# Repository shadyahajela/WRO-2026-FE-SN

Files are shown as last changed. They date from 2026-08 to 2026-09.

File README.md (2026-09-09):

Team Sub-Atomica
====

This repository contains the engineering documentation and our journey of building an autonomous vehicle to compete at the 2026 WRO Future Engineers competition.

<p align="center">


## Introduction

We are Team Sub-Atomica, Niva, Jeevesh and Shadya. We are united by a passion for STEM, Electronics, coding and jalapeño poppers. We wanted to bring our jouney to many others with the same passions and inspire teenagers around the world. To us its more than just coding or building, its the experiences and connections along the way.


159C16BD-3B52-4F8A-85BE-AFA5FE405926 (1)
IMG_6102 (1)

## Robot 

Our robot is called Jadoo which means magic in Hindi. The name comes from a popular movie character who is also an alien and can do Jadoo. The drive base of our robot kind of looked like an alien head, so we named it after our favorite alien character.

### Robot images







**Dimensions**

| **Specification** | **Measurement** |
|---|---|
| **Width** | 12 cm |
| **Length** | 23 cm |
| **Height** | 17 cm (Without wire) |
| | 20 cm (With Camera wire) |
| **Weight** | About 800 grams |
          
The Width helps to get around tight areas and the height gives a low base with a more balanced center of gravity all while being easy to maneuver due to the length. 

## Open challenge videos
Watch the video (https://www.youtube.com/watch?v=8OkpqqfYOhU)

## Obstacle challenge video
Watch the video (https://www.youtube.com/watch?v=r0wWpeo_AAc)

## Content

* `t-photos` contains photos of the team.
* `v-photos` contains 6 photos of the vehicle (from every side, from top and bottom)
* `video` contains the video.md file with the link to a video where driving demonstration exists
* `schemes` contains one or several schematic diagrams in form of JPEG, PNG or PDF of the electromechanical components illustrating all the elements (electronic components and motors) used in the vehicle and how they connect to each other.
* `src` contains code of control software for all components which were programmed to participate in the competition
* `models` is for the files for models used by 3D printers, laser cutting machines and CNC machines to produce the vehicle elements. If there is nothing to add to this location, the directory can be removed.
* `other` is for other files which can be used to understand how to prepare the vehicle for the competition. It may include documentation how to connect to a SBC/SBM and upload files there, datasets, hardware specifications, communication protocols descriptions etc. If there is nothing to add to this location, the directory can be removed.

# 1. Mobility Management

To build a self-driving car we need to build a car.

Objectives:

As per the rules, the car must have a steering mechanism and the rear axle driven by a motor.
Our team also wanted the car to be stable and fast (and colorful if we can help it).

## 1.1 Drive System
**Drive Motor:** JGA25-371 DC Motor with Hall-encoder. 
  <table>
  <tr>
    <td align="center" width="300" >
      
    </td>
    <td>
      <h3>Specifications:</h3>
      <ul>
        <li>Voltage: 12V </li>
        <li>No-load Speed: 620RPM </li>
        <li>Stall Torque: 4.2kg/cm</li>
        <li>Current: 0.046A</li>
        <li>Gear Ratio: 21.3:1</li>
      </ul>
    </td>
  </tr>
  </table>

 **Selection Reasoning** 

+ Built-in encoder, allowing for precise movement and less wiring hassle.
+ High torque for pushing the robot with vigor and avoiding stalling.

The JGA25-371 motor was selected because it combines high torque with integrated encoder feedback, providing both the power and precision required for the WRO Future Engineers competition. The 620 RPM gives enough torque to have a fast robot and have enough control for parking. We calculated torque required to pull our robot and to start it. Additionally the hall encoder provides real-time feedback for closed-loop control, allowing the robot to accurately measure wheel rotation, regulate speed, and maintain consistent movement especially during parking. 



*Image pinpoints exact location of torque calculations.(for full image look for Torque and speed reasoning)*
<br/>

 **Considerations:**
  An alternative would be a NEMA 17 stepper motor, which can provide precise speed and position control. However, the NEMA 17 is larger and heavier, and would require a more complex driver setup, making it less suitable for our robot. The JGA25-371 was chosen instead because it provides sufficient speed and torque while being more compact and easier to integrate.

### Differential

We used a metal WLTOYS 144001 differential in our robot, allowing the left and right rear wheels to rotate at different speeds during turns, reducing tire scrub and improving turning efficiency. This provides smoother cornering by distributing torque between both wheels and compensating for the different distances they travel. The differential improves maneuverability and stability during the Obstacle Challenge and parallel parking, where precise and repeatable movement is essential, while its metal construction provides durability under drivetrain loads.
  
  <table>
  <tr>
    <td align="center" width="300" >
      
    </td>
    <td>
      <h3>Specifications:</h3>
      <ul>
        <li>Differential Type: Planetary bevel-gear differential</li>
        <li>Material: Metal</li>
        <li>Application: 1:14 RC vehicles</li>
        <li>Drive Configuration: Rear-wheel drive</li>
        <li>Compatibility: 5 mm drive cups (custom coupled to LEGO axle)</li>
      </ul>
    </td>
  </tr>
  </table>

  **Mounting:**

  * Installed using an inset groove system in the chassis screwed to a detachable 3D-printed motor differential housing clamp that is placed above the differential gear compartment. This will allow for future changes to accommodate different motors and gears if the need arise.

    

  * Wires connected to Arduino Nano and Motor Driver.
  * Spike Prime wheels fitted onto the LEGO motor axle.

## 1.2 Steering System

**Steering:** Initially Parallel Steering, then changed to Ackermann Steering Geometry, prototyped with LEGO technic parts and later made with 3D printed parts. Ackermann was especially important for obstacle navigation and parking, where precise control and a small turning radius are essential. We also considered parallel steering because it was simpler to implement, but chose Ackermann as a calculated risk for its improved maneuverability. Our implementation uses a custom 3D-printed Ackermann steering mechanism, we used Onshape to experiment with different pivot points, linkage positions, and steering angles throughout the design process.

Through 2 iterations, we shortened both rods and increased the length of the side rods to achieve a smaller turning radius while keeping the mechanism compact. In our first iteration we made our tabs 2mm longer and the neck of the robot smaller, this gave us a 15 degree increase in our turning radius. We also experimented with shortening the rods to make our wheels streamlined and finalized with 9.53cm for the long shaft and 8.5cm for the short one. A major constraint was the chassis neck, which limited the steering angle because the wheels could collide with it. We therefore cut part of the chassis around the steering area to provide sufficient clearance.

**Calibration and Implementation:**
To achieve accurate and consistent steering, we used a combination of CAD adjustments and physical testing:

* Different servo positions, linkage lengths, and steering angles were tested in Onshape to determine the most suitable configuration.
* The physical steering assembly was then tested by turning the wheels fully in both directions and checking for smooth, consistent movement.
* Based on the test results, we modified the CAD model and repeated the process until the steering geometry provided the desired range of motion and wheel           alignment.
* The final Onshape design was then used to produce the 3D-printed steering assembly.





*This was an early prototype of the Ackerman Steering model before we added it to the first iteration of our Lego car chassis.*

### Steering Motor

We chose the MG90S Micro Servo for precise steering and weight reduction. The compact size and PWM interface make the MG90S easy to integrate and control using the Arduino Nano. It provides sufficient torque to steer the front wheels accurately and responsively. Its fast response and metal gear construction provide reliable and stable steering during turns and lane changes. The MG90S is widely used in hobby robotics, making replacement parts, mounting hardware, and documentation readily available. Additionally while testing it with our code for control we were able to make it work 90% of the time, upon investigating we found a fault with the power system in the testing module which we solved by adjusting our wires. 

  <table>
  <tr>
    <td align="center" width="300" >
      
    </td>
    <td>
      <h3>Specifications:</h3>
      <ul>
        <li>Voltage: 4.8V-6V </li>
        <li>Operating Speed: 0.1 s/60° at 4.8 V, 0.08 s/60° at 6 V</li>
        <li>Stall Torque: 1.8 kg·cm at 4.8 V, 2.2 kg·cm at 6 V</li>
        <li>Current: 0.010A</li>
        <li>Rotation Range: Approximately 180° (90° in each direction)</li>
      </ul>
    </td>
  </tr>
  </table>

**Mounting:**

* Screwed into a platform plate in front of the chassis, connected to the steering mechanism.

  

**Considerations:**
An alternative would be the MG996R servo, which provides higher torque and more durable metal gears. However, it is larger and requires more power than the MG90S, which would require modifications to our chassis and power system. The MG90S was chosen instead because it is more compact and sufficient for our steering system.

## 1.3 Chassis Design

| Dimension | Value (mm) | Reason |
| --- | --- | --- |
| Width | 120 | Component fit (Arduino, voltage converter and battery in line horizontally) |
| Length | 230 | Tight turns and component fit |
| Height | 200 | (Including camera wire) |

### Design Overview:

**Iteration 1: LEGO**






Aspects acheived:
* A functioning robot capable of performing the game to a certain degree of efficiency.
* Experiment with a new camera angle.                                     

Drawbacks:
* Tall and bulky design paired with a narrow body produced a high center of gravity and minimal support, making the robot unstable on quick turns and slower on straights.
* The low camera angle caused loss of depth perception, we we decided to completely reengineer it. 
* LEGO Technic design limited freedom of customizability, forcing any 3D printed parts to align to a LEGO frame.
* Limited range of movement for LEGO Ackermann steering system, constraining turns to 40 degrees to either side.
* Terrible tolerances (byproduct of using LEGO) result in constant plastic grinding in rear drive system.
* Inefficient component layout leaving much wasted space and area for drag

**Iteration 2: 3D Printed Parts and LEGO fusion:**



Aspects achieved/retained:
* Customizability of component mounting, such as custom in-built mounts for the IMU, DC Motor, etc.
* Expanded range of movement for newly 3D printed Ackermann steering system, allowing turns up to 55 degrees to either side.
* Improved tolerances and a switch from LEGO to metal differential remove the grinding in the read drive system.
* Optimized component layout for maximum space usage and minimal drag-creating parts.

Drawbacks:
* LEGO camera mount restrains pinpoint mount changes to find optimal camera angle.
* LEGO servo mount is unnecessarily complex and is not fixed precisely, allowing for small movements when the servo moves.
* Slightly imprecise tolerances for rear differential drive system, resulting in jerky movement and inconsistent torque and speed.

**Iteration 3: Fully 3D Printed Chassis:**



Aspects achieved/retained:
* 3D printed camera mount allows for custom mounting; iteration testing resulted in us finding the optimal camera angle and height.
* 3D printed servo mount is a simple, single piece mount that effectively zeros servo shaking.
* Perfected tolerances in the rear differential drive system allow the motor to turn the rear axle efficiently with little energy lost and constant torque and speed.
* Customizability of component mounting, such as custom in-built mounts for the IMU, DC Motor, etc.
* Expanded range of movement for Ackermann steering system, allowing turns up to 55 degrees to either side.
* Optimized component layout for maximum space usage and minimal drag-creating parts.

Accepted Trade-Offs:
* Overall shape of the robot is not streamlined and produces drag, but minimal enough that it barely affects performance.
* Minimal space for wire management, wires don't affect functions of the robot so its accepted.

Our chassis was designed on Onshape and printed using Carbon fiber, as it is light and resistant to snapping, which helps in thin and high tension areas like the neck of our robot. Other than the chassis itself the other 3D printed components use PLA and are designed on Onshape as well.

## 1.4 Torque and Speed reasoning



Our torque and speed reasoning lists the given parameters, we are able to calculate the max speed, the robots acceleration as well as the gives the minimum torque required to move our robot, allowing us to control speed. We are also able to calculate the cruising torque and stall torque which we used for selecting our motor. Based on our robot's total mass of 0.8 kg and wheel diameter of 0.056 m, we calculated a required motor torque of approximately 0.0117 N·m during acceleration, which is well within our motor's stall torque of 0.0833 N·m, giving a safety margin of roughly 7x (required torque is only ~14% of available stall torque).

# 2. Power Systems and Hardware Architecture

For the car to know what its doing, we need input and power.

Objective: 
  - Select the right hardware / electronic components for the entire sensor input processing and actuator control in real-time 
  - Supply adequate power to all these components

## 2.1 Power Source

**Battery:** 3 Cell Lithium Battery

<table>
  <tr>
    <td align="center" width="300" >
      
    </td>
    <td>
      <h3>Specifications:</h3>
      <ul>
        <li>Nominal Voltage: 11.1V</li>
        <li>Fully Charged Voltage: 12.6V</li>
        <li>Capacity: 3000 mAh</li>
        <li>Discharge Rate: 30 C</li>
        <li>Maximum Continuous Current: 90 A</li>
        <li>Battery Type: Lithium-Polymer</li>
      </ul>
    </td>
  </tr>
  </table>

The power system is essential to the robot’s ability to operate reliably throughout the competition. Our robot is powered by a 3-cell (3S) Lithium Polymer (LiPo) battery. The battery provides a nominal voltage of 11.1 V and a fully charged voltage of 12.6 V. Its high discharge capability allows it to supply sufficient current to the motors and other components. The battery’s high energy density provides a good balance between runtime, weight, and available power, making it well suited for a mobile competition robot. A rocker switch is connected directly to the power source independent of the code to switch on and off the robot. 

The JGA25-371 motor operate from the 12V supply provided by the battery, while the L298N motor driver regulates the power delivered to the motors based on commands from the Arduino Nano. The higher voltage of the 3S battery allows the motors to operate without requiring a step-up converter, simplifying the power system and reducing unnecessary conversion losses. A step-down converter is used to reduce the battery voltage to the appropriate levels required by the Raspberry Pi 5, Arduino Nano, camera, IMU, and other electronics. This separates the high-current motor supply from the lower-voltage electronics while allowing the entire robot to be powered from a single battery.

**Motor Driver:** L298N
  
  <table>
  <tr>
    <td align="center" width="300" >
      
    </td>
    <td>
      <h3>Specifications:</h3>
      <ul>
        <li>Driver Type: Dual H-Bridge</li>
        <li>Motor supply voltage: 5–35 V</li>
        <li>Maximum current: 2 A per channel</li>
        <li>PWM speed control</li>
        <li>Bidirectional motor control</li>
        <li>Overtemperature protection</li>
      </ul>
    </td>
  </tr>
  </table>

We chose the L298N motor driver because it provides reliable control of our JGA25-371 DC motor while being compatible with the Arduino Nano. It supports the 12V supply from our 3-cell LiPo battery and allows the Arduino to control motor direction and speed through its PWM inputs. This provides a simple and reliable connection between the robot’s power system and drivetrain, making it well suited for our differential drive system. The driver has a voltage drop in its internal transistors which causes us to not achieve its full potential, but we were willing to make a trade-off as we were content with what we were able to use it for.  

OLD MOTOR DRIVER IMAGE: DRV8871



We used DRV8871 in earlier iterations of the robot because of its compactness and its single motor control. However, it kept burning out due to motor feedback coming back to the driver. Motor feedback occurs when a motor is forced to move, and was probably caused by the constant pulling of the robot we did when testing. After further research, we found out that this feedback was a common problem with the DRV8871, so we decided to move to the L298N motor driver. Although it is much larger and bulkier, we had considerable space for the motor driver so it wasn't an issue. The L298N also has a heatsink, so overheating is not a problem.

## 2.2 Sensor and Camera
  
  **SainSmart Wide-Angle Camera:** 

  <table>
  <tr>
    <td align="center" width="300" >
      
    </td>
    <td>
      <h3>Specifications:</h3>
      <ul>
        <li>Resolution: 5MP (2592 × 1944)</li>
        <li>Image Sensor: OV5647</li>
        <li>Field of View: 160°</li>
        <li>Interface: CSI</li>
        <li>Video: 1080p @ 30 FPS, 720p @ 60 FPS, 640 × 480 @ 60/90 FPS</li>
        <li>Dimensions: 25 × 24 × 9 mm</li>
      </ul>
    </td>
  </tr>
  </table>

**Selection Reasoning:** 

- 160° wide field of view captures more of the course, reducing blind spots and improving environmental awareness.
- 5MP resolution provides enough detail to reliably distinguish course features and colored markers.
- 1080p at 30 FPS provides responsive visual data for real-time image processing and object detection.
- Compact and lightweight design reduces its impact on vehicle weight and balance while allowing flexible mounting.

This setup provides a 160° wide-angle view that increases the robot's visual coverage during both the Open Challenge and Obstacle Challenge. The camera supplies visual information about walls, pillars, colored markers, parking spaces, and lane lines, which is combined with other sensor data to support navigation and decision-making. The main tradeoff is balancing wider coverage with image processing requirements, so the selected resolution and frame rate provide sufficient detail and responsiveness without unnecessarily increasing processing demands.

The camera is mainly used for the following tasks:

- Detect and determine wall positions.
- Identify pillar colors and types.
- Recognize parking zones.
- Track path lines and boundaries.

**BNO055 Inertial Measurement Unit (IMU):** 

<table>
  <tr>
    <td align="center" width="300" >
      
    </td>
    <td>
      <h3>Specifications:</h3>
      <ul>
        <li>Sensor Type: 9-axis IMU (3-axis accelerometer, 3-axis gyroscope, 3-axis magnetometer)</li>
        <li>Processor: ARM Cortex-M0+ with integrated Bosch sensor-fusion firmware</li>
        <li>Interfaces: I²C, UART</li>
        <li>Operating Voltage: 3.3V</li>
        <li>Key Features: Absolute orientation, linear acceleration, gravity vector, magnetic heading, temperature sensing, and motion detection</li>
      </ul>
    </td>
  </tr>
</table>

**Selection Reasoning:** 

Considering we wanted to have a relative compass to reduce additional code in the Arduino, we chose the BNO055. The BNO055 is a compact 9-axis IMU that combines a3-axis accelerometer, 3-axis gyroscope, and 3-axis magnetometer with an onboard processor for sensor fusion. It provides orientation data such as heading,       Euler angles, linear acceleration, and gravity direction, reducing the need for complex external calculations.
    
We mounted the BNO055 near the center of the chassis to provide stable and consistent measurements. It communicates with the Arduino Nano through the I²C interface, continuously providing real-time orientation and angular velocity data. This helps the robot maintain an accurate heading and make smoother steering adjustments, which are especially important during obstacle navigation.  
  
## 2.3 Processing Units

**Single Board Computer: Raspberry Pi 5**

  <table>
  <tr>
    <td align="center" width="300" >
      
    </td>
    <td>
      <h3>Specifications:</h3>
      <ul>
        <li>Processor: Broadcom BCM2712</li>
        <li>CPU: Quad-core Arm Cortex-A76 (2.4 GHz)</li>
        <li>Power: 5 V / 5 A USB-C</li>
        <li>RAM: 8 GB LPDDR4X</li>
        <li>USB Ports: 2 × USB 3.0, 2 × USB 2.0</li>
        <li>Video Output: Dual micro-HDMI (60fps)</li>
      </ul>
    </td>
  </tr>
  </table>

*Subsystem Integration:*
The Raspberry Pi 5 acts as the robot’s primary processing unit, handling high-level decision-making, image processing, and sensor-data integration. Its processing capability allows it to run real-time vision, mapping, obstacle detection, and path-planning tasks while communicating with the Arduino Nano for low-level control.

*Hardware and Software Architecture:*
The Raspberry Pi 5’s quad-core Arm Cortex-A76 CPU and 8GB of RAM provide sufficient processing performance for the computational demands of the robot. Its compact form factor also allows it to be mounted directly onto the chassis without significantly increasing the vehicle’s size or weight. It communicates with the Arduino Nano through a serial connection, creating a modular architecture where high-level processing and low-level control are separated.

*Iterations and Trade-Offs:*
We initially tested a Raspberry Pi 4 to reduce power consumption, but testing showed that its lower processing performance caused slower image processing and reduced responsiveness during real-time vision and navigation tasks. We therefore changed to the Raspberry Pi 5, accepting higher power consumption in exchange for significantly improved processing performance and more reliable real-time operation.

*Risk Analysis and Reliability:*
Using the Raspberry Pi 5 reduces the risk of processing bottlenecks affecting navigation and vision performance. Separating high-level processing from the Arduino Nano’s low-level control also prevents computationally intensive tasks from directly interfering with motor and steering control, improving overall system reliability.

**Microcontroller:** Arduino Nano

  <table>
  <tr>
    <td align="center" width="300" >
      
    </td>
    <td>
      <h3>Specifications:</h3>
      <ul>
        <li>ATmega328P 8-bit microcontroller</li>
        <li>32 KB flash memory</li>
        <li>2 KB SRAM</li>
        <li>16 MHz clock speed</li>
        <li>22 multi-function I/O pins</li>
        <li>UART, I²C, and SPI communication</li>
      </ul>
    </td>
  </tr>
  </table>
  
*Subsystem Integration:* 

 The Arduino Nano was selected as the robot’s low-level controller to handle time-sensitive tasks such as motor control, steering, and encoder/sensor input. This architecture separates high-level decision-making from low-level control, allowing the Raspberry Pi 5 to focus on vision processing, navigation, and path planning while the Arduino maintains consistent motor and steering responses.

*Hardware and Software Architecture:*

The Arduino Nano communicates with the Raspberry Pi 5 through a serial connection, creating a modular hardware and software architecture. This reduced the risk of timing conflicts caused by running motor-control tasks alongside computationally intensive processes on the Raspberry Pi. It also allows each subsystem to be tested independently, making troubleshooting and future modifications easier. It also displays steering values on the 1.12" OLED screen, we use it for understanding what the robot is thinking and troubleshoot. 

*Iterations and Trade-Offs:*

Our initial design used a microbit, but research showed that the Arduino Nano offered greater flexibility for external hardware and simpler bidirectional communication with the Raspberry Pi 5. We therefore changed to the Arduino Nano, trading the microbit’s built-in buttons and LEDs for improved subsystem integration and expandability. The control system was then iteratively tested and adjusted to improve motor response, steering accuracy, and communication reliability. Using a dedicated microcontroller introduced additional hardware and communication complexity, but provided more predictable real-time control and reduced the dependence of critical drivetrain functions on the Raspberry Pi’s processing workload.

*Risk Analysis and Reliability:*

This subsystem architecture improves reliability by isolating critical low-level control from higher-level software. If the vision or navigation software requires significant processing, the Arduino can continue executing motor and steering commands without relying on continuous high-level computation. This separation therefore supports more consistent movement and provides a more robust architecture for the challenges defined by WRO Future Engineers.

**Expansion Board:** Arduino Nano Shield

  <table>
  <tr>
    <td align="center" width="300" >
      
    </td>
    <td>
      <h3>Specifications:</h3>
      <ul>
        <li>Interface: Arduino Nano-compatible pin headers</li>
        <li>Supported Devices: Arduino Nano and compatible modules/sensors</li>
        <li>I/O Access: Digital, analog, PWM, UART, I²C, and SPI pins</li>
        <li>Power Supply: 5V and 3.3V power outputs</li>
      </ul>
    </td>
  </tr>
  </table>

  * The Arduino Nano Shield expands the robot’s capabilities by providing a convenient platform for connecting and controlling external components such as motors, sensors, and other peripherals.
  * It simplifies wiring by providing accessible connection points for the Arduino Nano’s input and output pins, while also supporting power distribution to connected components.
  * This makes the system easier to assemble, maintain, and modify, while providing reliable connections between the Arduino Nano and the robot’s hardware.

## 2.4 Circuit Diagram

  **Wiring Diagram:**

  Wiring Diagram (2)

  The Wiring diagram shows the connections to the different components that are located in the robot.
  
## 2.5 Power Consumption

| Component | Supply (V) | Typical Current (A) | Peak Current (A) | Typical Power (W) |
|---|---|---|---|---|
| Raspberry Pi 5 | 5 | 0.80 | 5.00 | 4.00 |
| Arduino Nano | 5 | 0.019 | 0.030 | 0.095 |
| 5MP SainSmart Wide-Angle Lens Camera | 5 | 0.15 | 0.25 | 0.75 |
| BNO055 IMU | 3.3 | 0.012 | 0.015 | 0.04 |
| Micro Servo MG90S (steering) | 5 | 0.20 | 0.80 | 1.00 |
| JGA25-371 DC Motor | 12 | 0.50 | 2.00 | 6.00 |
| L298N Motor Driver | 12 | 0.02 | 0.04 | 0.24 |
| Arduino Nano Shield | 5 | 0.019 | 0.030 | 0.095 |
| Step-Down Converter | — | — | — | η ≈ 88% |

## 2.6 Power System Architecture

This diagram shows how the 12V battery supplies power to the DC motor through the motor driver, and the step down buck converter which them supplies 5V power to the rest of the components. 



## 2.7 List of Components

| Major components | Reference Cost in CAD<br>\- As of Sep 1, 2026<br>\- Taxes not included | Purchase Link for Future Reference |
| --- | --- | --- |
| Raspberry Pi 5 4GB | $153.95 | [pishop.ca](https://www.pishop.ca/product/raspberry-pi-5-4gb) |
| Arduino Nano | $27.19 | [Amazon.ca](https://www.amazon.ca/dp/B0F6Y7GS4Q) |
| Arduino Nano Expansion Board | $13.99 | [Amazon.ca](https://www.amazon.ca/dp/B08198MSJ2) |
| 1.3" OLED display module SH1106 128x64 | $5.33 | [aliexpress.com](https://www.aliexpress.com/item/1005006827988792.html) |
| Sainsmart Wideangle 5MP Camera 160 degree FoV (OV5647 sensor) | $12.91 | [Amazon.ca](https://www.amazon.ca/SainSmart-Fish-Eye-Camera-Raspberry-Arduino/dp/B00N1YJKFS)  |
| Adafruit 9-DOF Absolute Orientation IMU Fusion Breakout - BNO055 | $38.38 | [Aliexpress.com](https://www.aliexpress.com/item/1005010734176030.html) |
| 12V Battery | $27.99 | [Amazon.ca](https://www.amazon.ca/12V-2800mAh-Rechargeable-Battery-Replacement/dp/B0FJ27ZT28) |
| 12V to 5V Step-down converter (XL4015 with Display) | $4.80 | [aliexpress.com](https://www.aliexpress.com/item/1005008401247033.html) |
| JGA25-371 620 rpm 12V Brushless DC motor with Encoder | $12.78 | [aliexpress.com](https://www.aliexpress.com/item/1005007546764319.html) |
| WItoys 144010 Metal Differential Gearbox | $40.58 | [aliexpress.com](https://www.aliexpress.com/item/1005005869550963.html) |
| L298N Motor Driver | $11.99 | [Amazon.ca](https://www.amazon.ca/dp/B0D8G2PZBB) |
| MG90S Servo motors | $17.02 | [Amazon.ca](https://www.amazon.ca/dp/B0BWJ4RKGV) |
| Short USB to USB-C cable | $11.39 | [Amazon.ca](https://www.amazon.ca/dp/B0DG8J6S1G) |
| Rocker Switch | $2.65 | [aliexpress.com](https://www.aliexpress.com/item/1005007044175800.html) |
| Push Button breakout module | $1.52 | [aliexpress.com](https://www.aliexpress.com/item/32820437436.html) |
| Lego wheels, axles and connectors | $50.00 | Approximately |
| 3D printed parts for the chassis | $25.00 | Approximately for one spool of PLA filament |
| Total | $473.49 | |

# 3. Software Architecture

## 3.1 Code Origins
Following our research of other teams our exploration of software development had humble origins since many of the concepts required to build and program an autonomous vehicle were new to us.

1. Started with just a raspberry pi and a wide-angle camera to detect walls and objects
2. Added proportional steering angle calculation to drive a virtual servo
3. Had a Micro\:bit microcontroller connected to the Raspberry Pi over USB for serial connection, and coded it to receive the servo values from the Pi to drive an actual servo
4. Added a DC motor and driver to the microcontroller for vehicle movement, and ensured all of these worked in tandem
5. Put this entire setup on a Lego chassis for iteration 1 
6. Tested this iteration on a table-top test bench made out of Lego with actual walls and 3 printed color blocks to tune the steering values for walls and obstacles.
7. We then changed to Arduino since it was harder to connect components to a Micro\:bit directly and the expansion board we used had problems driving the servo motor consistently

## 3.2 Open Challenge Algorithm

We started by defining a Frames class which 

- Encapsulated a Region of Interest (ROI) 
- Initialization included defining the boundary coordinates of the ROI and the colors it must be able to detect
- Had functions to return all the colored pixels matching a specific color range in HSV, return contours by matching adjacent colored pixels, return the biggest contour, return the area of all contours

### 3.2.1 Iteration 1

We spent a lot of time in open challenge iterations since the idea was to have a solid foundation for obstacle challenge. The frames class and the state transitions must be reusable for obstacle challenge where needed
Iteration 1 had 2 distinct states

- STRAIGHT - Drive the robot straight following the walls
- TURN - When a colored line is seen, check if it is safe to turn and perform a timed turn

**MAIN LOOP**

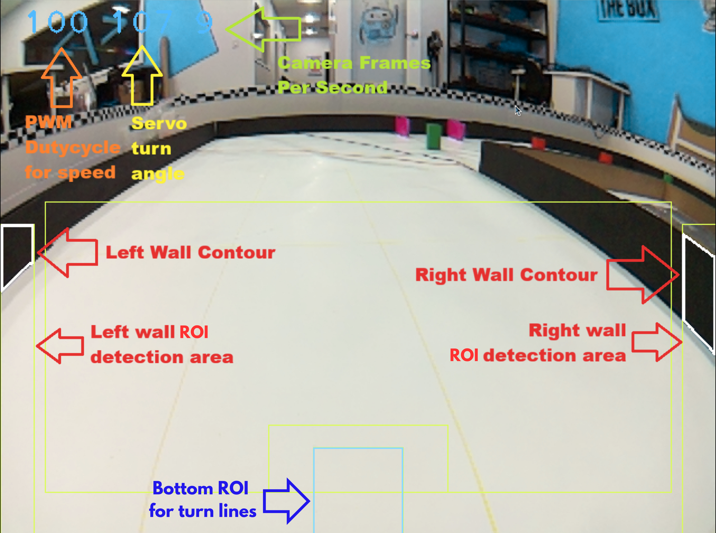
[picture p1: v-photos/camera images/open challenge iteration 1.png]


- Two rectangular ROIs placed on the left and right sides of the frame, each able to detect black colored pixels
  - Keep a record of the number of black pixels detected within each ROI which represent how much of the inner and outer walls are visible to the camera on each side
- One rectangular ROI placed on the bottom of the frame to detect orange and blue colored pixels > 200 (to avoid detecting noise)
  - If Orange was detected first, set direction to clockwise (CW) for the robot to travel
  - If Blue was detected, set direction to counter-clockwise (CCW)
  - As soon as a colored line is detected, since it may take several frames to pass over that line, use a timer to avoid reading the same line again
  - Keep track of number of orange and blue lines crossed
- If colored line was detected
  - If there is no wall in the direction of travel, initiate TURN state
- Else
  - Initiate STRAIGHT state
- If the number of lines passed > 12, stop the robot after a fixed time (depending on speed) to position it in the starting section
- Compute steering value, speed, a direction value (forward/reverse/stop, chosen by the Pi based on what the vehicle currently needs to do), the current lap-line count, and the current state are packed into a single message and sent over USB serial (19200 baud) to an Arduino Nano, which handles the physical motor and servo output

**STRAIGHT**
<br/>
- `Steering error` was calculated as `right-side black pixel count - left-side black pixel count`
- If `Steering error` was positive 
  - This means more wall visible on the left 
  - Vehicle should steer right
- If `Steering error` was negative
  - This means more wall visible on the right
  - Vehicle should steer left
- The steering should be proportional to the error, so a simple proportional (P) controller was used meaning the steering angle was simply the error multiplied by a constant gain value (KP),  the further off-center the pixel counts were, the harder the robot steered
  - KP constant is simply calculated by scaling the error down to the range of the steering margin (45)
  - In this case, the error was in the range of 6000 pixels nominally
  - So we started with a KP of 30 / 6000 = 0.005 and then tuned it from there
- In summary `Steering angle = Steering error * kp`

**TURN**

- If a `wall missing` condition is detected in the direction of turn, turn steering hard for a fixed amount of time.
  - No feedback mechanism was used for the turn 
- The time was tuned until the turn completed properly 

**Observations and improvements made**

- Problem: Bright lighting conditions caused the pixel detection to be fuzzy
  - **Idea implemented**: Lowered the camera angle by about 8 degrees so as to catch less of ambient light while still being able to see the walls
- Problem: It would be ideal for a vehicle to travel closer to the inner wall to save time. However, if the algorithm just measured raw pixels on either side, a robot pointed straight but traveling closer to one wall would report a large error even though no correction was actually needed.
  - **Idea implemented**: Add an offset to the pixel count on the outer perimeter to guide the robot to run close to the inner wall
  - **Idea for next iteration**: Alternatively, derive the wall geometry/position rather than raw pixel volume, so the vehicle would travel straight regardless of the robot's exact distance from a wall or the lighting conditions on a given day
- Problem: While a simple proportional (P) controller was mostly sufficient, the robot steering wasn’t as smooth as we wanted it to be, especially after completing a turn. 
  - **Idea for next iteration**: Add a Derivative (D) to the controller which would account for the rate of change of error to damp out sudden changes in steering and make for smoother steering

### 3.2.2 Iteration 2

**STRAIGHT**

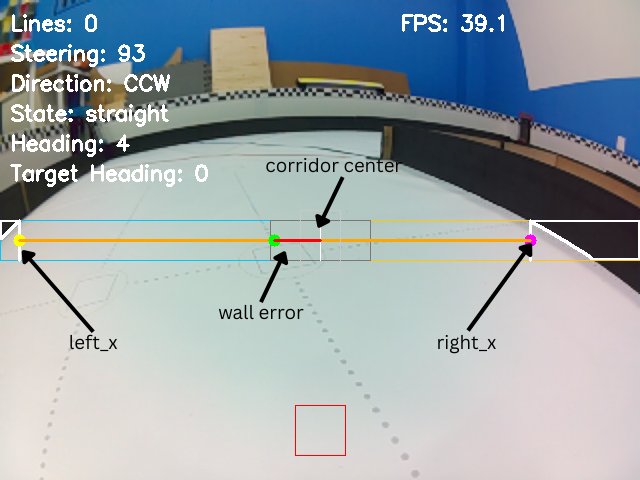
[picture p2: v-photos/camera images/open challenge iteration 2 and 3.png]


- Replaced the two side ROIs with a single thin horizontal ROI band closer spanning the full width of the frame. This ROI was placed just at the vertical center so the algorithm can sufficiently look ahead to calculate steering
- Scans inward from each edge of the ROI to find the nearest wall pixel on the left half and the nearest wall pixel on the right half, on the same row, marking each as a boundary point
- If a wall drops out of frame, the boundary point is simply the far edge of the ROI on that side
- The midpoint between the two boundary points is the "path center"
- The horizontal offset between this path center and the frame's true horizontal center is the steering error
- A small dead zone (±20px) is applied around the centered wall-following error, errors inside this band are treated as zero, preventing constant tiny steering corrections once the robot is already well-centered

* Added a derivative term to the corridor-center error, moving from P to PD control: `control_signal = (kp × error) + (kd × (error − previous_error))`
  - The derivative term reacts to how quickly the error is changing frame to frame, which damps the overcorrection behavior from Iteration 1 and produces a visibly smoother line, especially noticeable at higher driving speeds where a pure-P response tends to overreact to small changes

**TURN**

- A turn only actually triggers after the line-detected + wall-missing condition holds continuously for a short confirmation window (0.15s), rather than on the first frame it's seen. This prevents the robot from running into corners

**Observations and improvements made**

- Problem: Timed turns still needed per-corner retuning, since the inner wall's length and shape vary between corners depending on the round's randomized wall configuration,  a duration tuned for one corner would overshoot or undershoot the next. Turn duration also drifted over the course of a run as battery voltage sagged and motor speed dropped slightly, or if the wheels lost grip occasionally. Duration of turn had to be adjusted every time we had to change the speed of the robot for testing
  - **Idea for next iteration**: Use a feedback mechanism to detect when a turn ends and implement a PD controller

### 3.2.3 Iteration 3 (Current)

**MAIN LOOP**

- Added an IMU (BNO055) to track heading (0–360°)
  - Note: We built a utility program [bno055.py](https://github.com/shadyahajela/WRO-2026-FE-SN/blob/main/src/sensor/bno055.py) to calibrate and test the BNO055 IMU sensor. The IMU integration was also tested on the table-top test bench and tuned before the robot was tested on the field
- Reset heading to 0 at startup
- Each time a colored line is passed, a turn counter increments, and the target heading is set as an **absolute** multiple of 90°,  `turn_count × 90°` (mod 360°, sign flipped for CCW),  rather than the previous target plus 90°. This is to ensure small heading errors from one turn can't accumulate and drift into the next turn's target

**TURN**

- `Turn error` is the shortest signed angular distance between target and current heading (normalized to −180°…180°, so the robot always turns the short way)
- `Steering value = turn error * kp_turn`

- `kp_turn` is the proportional gain constant for  proportional (P) control, consistent with the steering approach used elsewhere in the system
- The turn is considered complete once heading error is within 2°, at which point the robot returns to STRAIGHT and resets its tracking flags

<table>
  <tr>
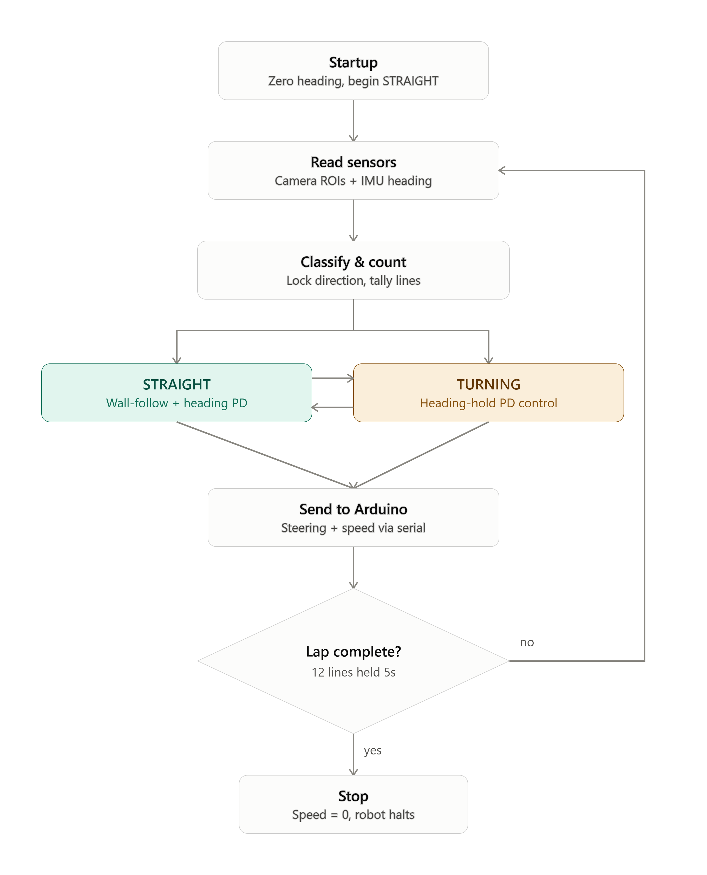
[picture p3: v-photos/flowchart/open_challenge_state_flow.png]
    <td align="center"><strong>Flowchart - Open Challenge</strong><br/></td>
  </tr>
</table>

## 3.3 Obstacle Challenge Algorithm

**Pass rule:** green blocks are passed on the left, red blocks are passed on the right.

### 3.3.1 Iteration 1 - Treating Obstacles as Virtual Walls

**Approach**

- Reused the Open Challenge STRAIGHT corridor-centering algorithm rather than building separate obstacle-handling logic
- Red is passed on the right, so a detected red block sits to the robot's left as it passes,  its bottom-right corner (the edge nearest the robot's path) was fed in as a substitute **left-wall** boundary point
- Green is passed on the left, so a detected green block sits to the robot's right as it passes,  its bottom-left corner was fed in as a substitute **right-wall** boundary point
- The corridor-center calculation then treated that corner exactly like a real wall-edge point, steering around it the same way it would steer around a wall

**Issues**

- The corridor-centering math was tuned for two continuous, roughly parallel wall surfaces,  a single point from a small discrete block gave a much shakier corridor estimate, since the "wall" on that side was only a few centimeters wide instead of an extended surface
- With only one corner representing the whole block, the estimated boundary jumped noticeably frame to frame as viewing angle changed on approach, so steering reacted inconsistently to what should have been a smooth approach
- No explicit sense of distance to the block,  correction strength was identical whether the block was far away or dangerously close, since wall-following gains (tuned for gradual convergence) were being reused for what should've been a more urgent, close-range maneuver
- Blocks near a real corner or wall created ambiguity about which "wall" the algorithm was actually reacting to, occasionally steering toward the block instead of away from it

**Why We Improved**

- Needed obstacle avoidance treated as its own problem with its own reference points, not a block disguised as a wall
- Needed distance to the block to explicitly scale the strength of the correction, not just its direction

### 3.3.2 Iteration 2,  Dual-Axis "Pulling" Control

<table align="center">
  <tr>
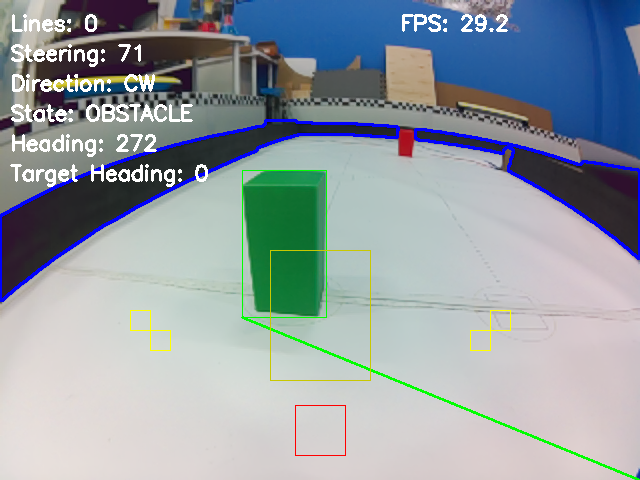
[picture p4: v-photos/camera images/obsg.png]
    <td align="center"><strong>Parking clockwise</strong><br/></td>
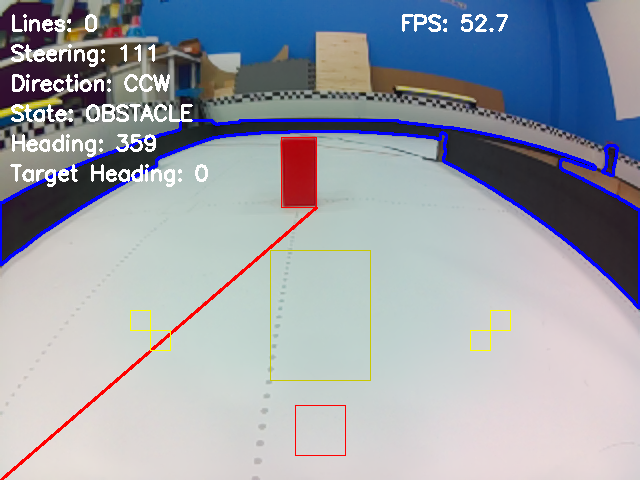
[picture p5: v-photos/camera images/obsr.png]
    <td align="center"><strong>Parking counter-clockwise</strong><br/></td>
  </tr>
</table>

**Approach**

- Green block: reference dot at the block's bottom-left corner, fixed target dot at the bottom-right corner of the screen
- Red block: mirrored,  reference dot at the block's bottom-right corner, fixed target dot at the bottom-left corner of the screen
- Horizontal (x) offset between reference and target dots drives a PD controller,  correction is added to center for red (steers right) and subtracted for green (steers left)
- Vertical (y) offset doesn't drive steering directly,  it produces a distance falloff factor that scales the whole PD correction: strongest as the block's bottom edge nears the bottom of the frame (close), fading toward zero as it sits higher in the frame (far). This is exactly what Iteration 1 was missing
- Overall effect is like an elastic band strung between the two dots,  as the robot approaches, the "pull" tightens and the correction strengthens, instead of a constant-strength nudge regardless of distance
- Falls back to the same corridor-centering wall-following logic from Open Challenge whenever no block is visible, but with its own separately tuned gains,  Obstacle Challenge's field and required correction strength weren't identical to Open Challenge's, so tuning each independently gave a tighter fit for both
- If both a red and green block are visible in the same frame, only the physically nearer one (by vertical offset) is used to compute steering that frame,  the farther block is detected but ignored until it becomes the closer one
- Steering output is clamped to the same safe range used everywhere else in the system

**Issues**

- Inherited the same timed-turn unreliability as Open Challenge Iteration 2,  turn duration needed per-corner retuning and drifted with battery voltage and wheel grip over a run

**Why We Improved**

- Wanted the same closed-loop, drift-independent turning fix already validated in Open Challenge Iteration 3

### 3.3.3 Iteration 3 (Current),  IMU Heading-Based Turns

**Approach**

- Kept the Iteration 2 dual-axis pulling logic and wall-following fallback unchanged
- Replaced the fixed-duration turn with the same IMU heading-based approach as Open Challenge,  absolute cardinal target headings, incremented 90° per corner, closed-loop control to close the heading error, exiting once within tolerance rather than after a fixed time
- Mid-turn bail-out preserved: if a red or green block becomes visible above threshold while still turning, the robot exits the turn immediately and hands back to obstacle avoidance that same frame,  reacting to a visible block takes priority over finishing a scheduled turn

**Issues Resolved**

- Turning no longer depends on constant motor speed, wheel grip, or battery voltage, and generalizes across corner shapes without retuning
- No fixed duration to separately tune for Obstacle Challenge's corner geometry, since heading is now the closing condition

### 3.3.4 State Machine

Same two core behaviors as Open Challenge (wall-following and turning), with additional states layered in for obstacles, wrong-side blocks, and parking:

- **LEAVE**,  starting state; drives straight out of the parking bay, then hands off to normal driving once clear
- **STRAIGHT**,  corridor-centering wall-following; active by default whenever no red/green block is visible
- **OBSTACLE**,  dual-axis pulling control; active by default whenever a red or green block is visible
- **TURNING**,  IMU heading-based turn triggered at a lap line; exits early back to OBSTACLE if a block becomes visible mid-turn, otherwise exits to STRAIGHT once heading target is reached
- **OBS\_CRITICAL**,  triggered by spotting a "wrong-side" block early, near an upcoming turn; holds a near-straight course via IMU-held heading until a threshold amount of wall fills the center of the frame, then forces a hard turn for a fixed duration to physically clear the block, then resumes normal driving
- **BETWEEN**,  entered after an OBS\_CRITICAL sequence completes near the end of the run; treats every remaining block as if it were red regardless of actual color, and watches for the parking wall to appear
- **PARK**,  final state; speed and steering held at rest

### 3.3.5 PARKING

Parking state initiates when the 12th floor line is read. Parking is achieved by 5 distinct maneuvers explained below

<table>
  <tr>
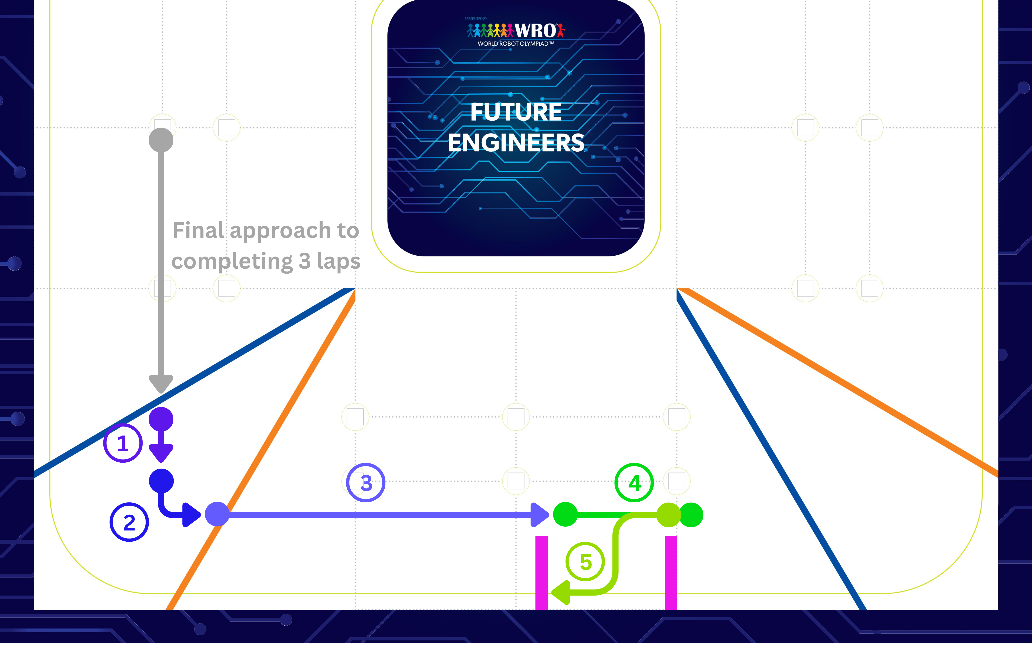
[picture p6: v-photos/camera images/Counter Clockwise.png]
    <td align="center"><strong>Parking counter-clockwise</strong></td>
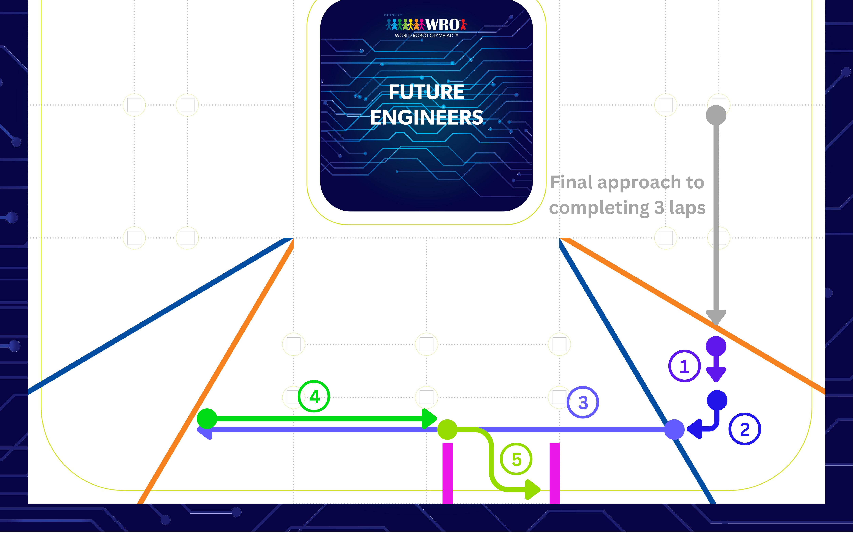
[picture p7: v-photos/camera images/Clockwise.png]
    <td align="center"><strong>Parking clockwise</strong></td>
  </tr>
</table>

1. Continue straight (IMU guided) until a small ROI detect the wall ahead to stop the robot at a fixed position 
2. Turn 90 degrees (IMU guided) in the direction of the parking blocks
3. a - Counter Clock-wise: Continue straight ahead towards the parking blocks by following a fixed offset against the wall until the robot positions just before  the first parking block which detects magenta pixels in an ROI on the center right
3. b - Clock-wise: Continue straight ahead towards the parking blocks by following a fixed offset against the walls until the robot sees the orange turn line in the bottom ROI
4. a - Counter Clock-wise: Move forward fixed distance until the robot is just after the second parking block
5. b - Clock-wise: Move reverse until the second parking blocks comes into view. Then move forward fixed distance until the robot is just after the second parking block
6. Execute a timed reverse double turn into the parking area similar to we perform parallel parking in real life

<table>
  <tr>
    <td align="center"><strong>Parking clockwise</strong><br/>
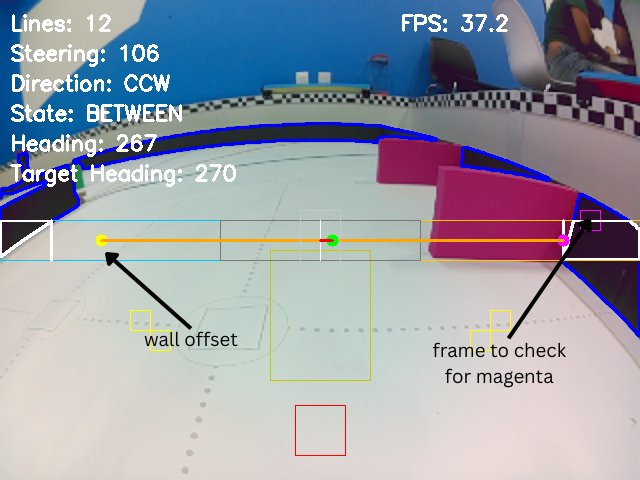
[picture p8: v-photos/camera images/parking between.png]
    </td>
  </tr>
  <tr><td>Above image shows Step 3 of parking where the robot has guided itself following the fixed offset off the wall (in the left, in this case) and using the magenta ROI (on the right, in this case) to position itself close to the first magenta block</td>
  </tr>
</table>

### 3.3.6 Edge Case Handling

**Prevent accidental running into walls**

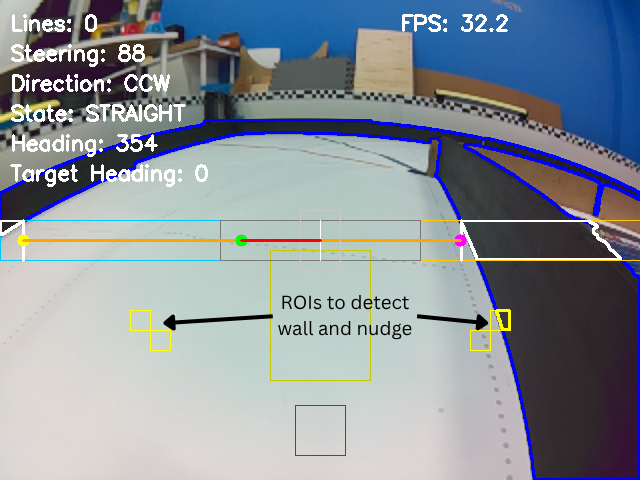
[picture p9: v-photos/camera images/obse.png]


- Independent of whichever behavior is currently driving steering, 2 small square ROIs arranged diagonally on either sides check how "full" of wall color they are
- A fully filled side nudges steering away from it more strongly than a partially filled reading; this correction is added on top of the frame's already-computed steering value, before the final clamp
- This logic runs on top of and independent of primary steering decision in every frame except while parked, acting as a standing safety margin against running into a wall or cutting a corner too tightly

**Navigating an obstacle when it is too close to the wall ahead**

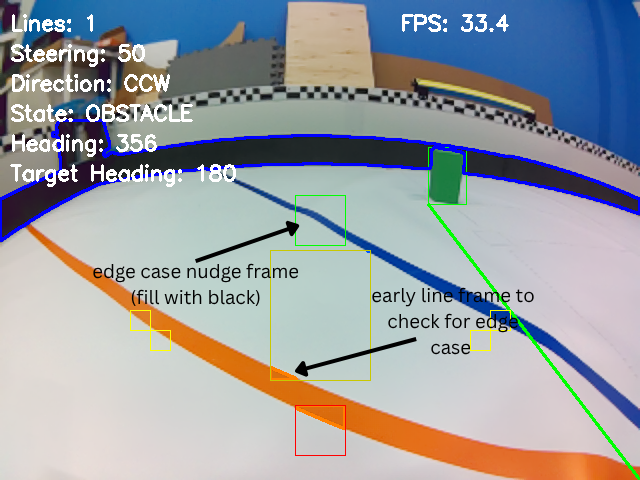
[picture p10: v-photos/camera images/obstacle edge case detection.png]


- This logic runs when the "early line ROI" detect a colored floor line and when a specific block (Green during Counter Clockwise and Red during Clockwise) is detected ahead which would make it difficult for the robot to navigate between the wall ahead and the block
- When this condition is met, the robot drives straight ahead until the nudge ROI is filled with black and the color block is not in view anymore
- Then robot executes a turn in the direction of travel until the nudge ROI does not see black 

## Microcontroller Code (Arduino Nano)

**Role**

- The Arduino Nano is the low-level hardware controller: it receives one serial command per frame from the Raspberry Pi and converts it into actual electrical signals for the drive motor, steering servo, an OLED status display, and a NeoPixel LED strip
- The Pi handles all vision processing and decision-making, including which direction the vehicle should currently be driving; the Arduino has no awareness of *why* a command was sent, only how to execute it
- We built a utility program [pi2nano_bi_test.py](https://github.com/shadyahajela/WRO-2026-FE-SN/blob/main/src/test/pi2nano_bi_test.py) to rigorously test the transmission of robot control data (servo angle and steering, newline \n delimited) to Arduino over serial connection. This program helped us identify that 30 millisecs is the minimum time between the Pi transmitting control data over USB serial connection and for the Arduino to finish processing it. If the data transfer is any faster (irrespective of whether the standard USB or USB 3 port was used), Arduino won’t be ready to receive the next byte stream over serial connection - even with non-blocking code. This would cause the outgoing message flush to fail on the Pi and if left unhandled, it would kill the challenge program

**Communication Protocol**

- Listens on serial at 19200 baud, matching the Pi's configured rate
- Reads one line at a time into a fixed 20-byte buffer via `readBytesUntil('\n', ...)`, null-terminating it once a full message arrives,  the fixed buffer size is a deliberate guard against uncontrolled memory allocation on a small microcontroller
- Expected message format: `steering speed direction lineCount state` (e.g. `110 255 1 12 OPEN`), parsed in one call with `sscanf`
- `direction` (0 = stop, 1 = forward, 2 = reverse) is actively chosen by the Pi each frame based on what the vehicle currently needs to do, not a fixed constant,  the Arduino simply executes whatever direction it's told
- The Arduino also talks back to the Pi: when the physical start button is pressed, it sends a plain `"START"` line over the same serial connection, with a short debounce delay

**Steering & Motor Control**

- Before applying anything, the received `servo` value is range-checked (`30 < servo < 160`),  if it falls outside this window, the entire steering + motor update is skipped for that frame, acting as a basic sanity check against corrupted or garbled serial data rather than driving on a bad command
- If valid, steering is applied first (`myservo.write(servo)`), then motor output, so both actuators respond to values from the same command packet rather than a mix of an old and new one
- Motor control goes through the L298N driver: `speed` (0–255) is written as a PWM duty cycle via `analogWrite`, while `direction` sets two digital direction pins,  forward and reverse drive the pins in opposite states, and stop (or an out-of-range `direction` value) sets both pins low, cutting drive entirely regardless of speed

**Status Display (OLED)**

- A 128×64 monochrome OLED (SH1106 driver, addressed over I²C) shows live telemetry every frame: current steering angle, line/lap count, motor speed, the current challenge state string, and a directional indicator (`>>` / `<<` / `XX`) showing forward, reverse, or stopped,  laid out in a fixed grid with divider lines, intended for operators to diagnose communication or control issues during testing at a glance

**LED Strip Status Indicator**

- An 8-pixel NeoPixel strip gives an at-a-glance visual state readout without needing to read the OLED up close: intended to show white for the OPEN challenge state and red otherwise
- **Known issue:** the state check currently compares the character array directly (`state == "OPEN"`) rather than with `strcmp()`, which compares memory addresses rather than string contents in C/C++ and will essentially never evaluate true,  the code already carries a comment flagging the correct fix, but it hasn't been applied yet, so in practice the LED likely always shows red regardless of actual state
- A full rainbow sweep runs once at boot as a power-on self-test, and both end pixels turn green once initialization completes, signaling the robot is ready to start

**Startup Sequence**

- On boot: configure pins, attach the servo, open serial, initialize the OLED and show a "BOOTING" message, initialize the LED strip, sweep the servo through a small range as a functional check before returning it to its calibrated center, run the rainbow self-test, then display "-READY-" and light the ready-indicator LEDs

# 4. 3D Model Files

## 4.1 Onshape CAD

We used Onshape to design the 3D models used to make the robot. The files can be found here (hyperlink).

## 4.2 STL Files

Below are the the STL files which are used in building the robot, which can be downloaded and 3D printed. Refer to detailed [step-by-step instructions](Build_Instructions.md) to reproduce the chassis of the robot and assemble all the components on it.  

**Chassis and Core Structure**

- [`BasePlateV8.stl`](mech/3D_CAD_Files/BasePlateV8.stl)

**Steering Linkages**

- [`AckermannLRodV3.stl`](mech/3D_CAD_Files/AckermannLRodV3.stl)
- [`AckermannSRodV2.stl`](mech/3D_CAD_Files/AckermannSRodV2.stl)
- [`DirectionTabsLH.stl`](mech/3D_CAD_Files/DirectionTabsLH.stl)
- [`DirectionTabsRH.stl`](mech/3D_CAD_Files/DirectionTabsRH.stl)
- [`AckermannHexaRod.stl`](mech/3D_CAD_Files/AckermannHexaRod.stl)

**Motor and Transmission**

- [`DifferentialHousingV4.stl`](mech/3D_CAD_Files/DifferentialHousingV4.stl)

**Wheel and Axle Components**

- [`Axle Spacer.stl`](mech/3D_CAD_Files/Axle_Spacer.stl)

**Mounting Components**

- [`CameraMountV3.stl`](mech/3D_CAD_Files/CameraMountV3.stl)
- [`MidPlateV2.stl`](mech/3D_CAD_Files/MidPlateV2.stl)
- [`PiPlateV3.stl`](mech/3D_CAD_Files/PiPlateV3.stl)
* Servo Box Mount (link)

**Coupling Parts**

- [`MotorDifferentialCoupling.stl`](mech/3D_CAD_Files/MotorDifferentialCoupling.stl)
- [`DifferentialAxleCoupling.stl`](mech/3D_CAD_Files/DifferentialAxleCoupling.stl)
* Servo-Axle Coupling (link)

**Miscellaneous**

- [`GuideArrowV3.stl`](mech/3D_CAD_Files/GuideArrowV3.stl)
- [`Battery_Holder.stl`](mech/3D_CAD_Files/Battery_Holder.stl)

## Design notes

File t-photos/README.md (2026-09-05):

Team's photos
====


IMG_6067 (2)



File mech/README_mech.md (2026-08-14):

# **Mechanical Design Process**
## **1. Rudimentary/Fundamental Mechanical Choices**

1.1 Wheel Choice

We chose Spike Prime wheels (56mm diameter, 14mm thickness) for their compactness, grip on vinyl, and familiarity. Larger wheels would make the robot harder to control and take too much space while smaller wheels would complicate the design and lower ground clearance. (PARAPHRASE!!!!!)

[insert image of Spike Prime wheel]

1.2 Steering System

**Prototype:** Our first prototype was a parallel steering system that used a servo mounted directly on the axle. It had issues with drifting on turns because both wheels were turning on the same radius, making their extension lines parallel so there is no instant center.


**Ackermann Steering:** We built an Ackermann Steering System to solve the drifting problem. An instant center is found where both wheels can rotate around with two different turn radii. The final iteration is 3D printed to accommodate the chassis base plate. The joints are joined using flat screws and locktight nuts, ensuring a tight fit while allowing full range of movement.


1.3 Rear Axle Differential

A physical differential composed of metal gears and casing allows the rear wheels to turn at different speeds to avoid wheel skipping when turning corners. Using a prioritization model, we concluded that printing our own gears would have a low Value vs. Complexity Ratio, and would not have provided such compact and smooth movement.

1.4 Dimensions Reasoning

Factoring in all the components we would need to fit on the chassis (Raspberry Pi 5, Arduino Nano, Motor, Step-Down Voltage Converter, ...), we decided to have a minimum width margin of approximately 30mm margin, meaning maximum 130mm. After testing multiple dimension iterations, we decided to make the robot about 230mm long and 120mm wide. We decided on these dimensions based on results of tests that focused on efficiently getting around tight edges, keeping balanced center of gravity (to avoid tipping and stay stable on sharp turns), and overall maneuverability. We had to take into account the large turning radius that a car with this length/width ratio has, similar to a go kart, and change our turning radius accordingly to leave minimal room when turning around pillars and corners.

## **2. Structural Prototypes**

+ **LEGO Prototype:** son
+ **Differential and Motor Positioning:** Motor positioned in the center of the base, axle connected to differential with custom coupling.
+ **Wheel Steering System:** Neck was made narrow to allow for greater steering range / turn radius.
+ **Base Layer:** Held drive motor, differential, servo, battery, and motor driver.
+ **Mid Plate:** Held Step-Down voltage converter and Arduino Nano.

## **3. Final 3D Printed Chassis**

## **4. Custom Mounts and Coupling**

+ Custom CAD designed holders for servo, raspberry pi, and camera

+ Motor coupler connects motor to differential


+ Servo coupler connects servo to Ackermann steering arm

+ Differential coupler connects servo to wheel axle


+ VEX standoffs, nuts, bolts, and locknuts

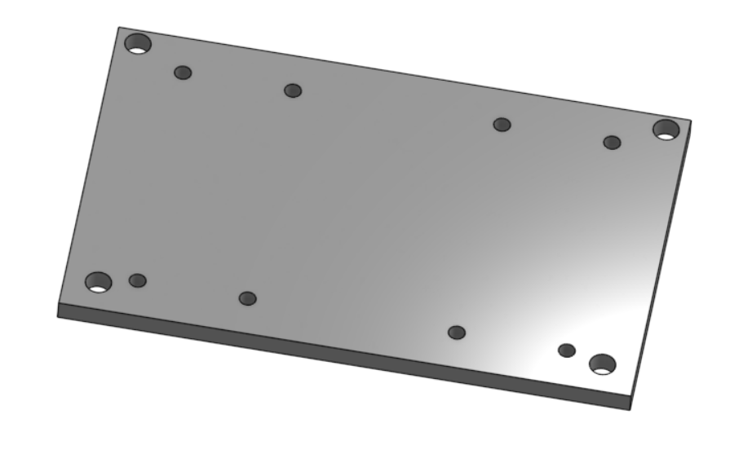
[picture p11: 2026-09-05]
mech/3D_CAD_Files/PiPlateV3.png

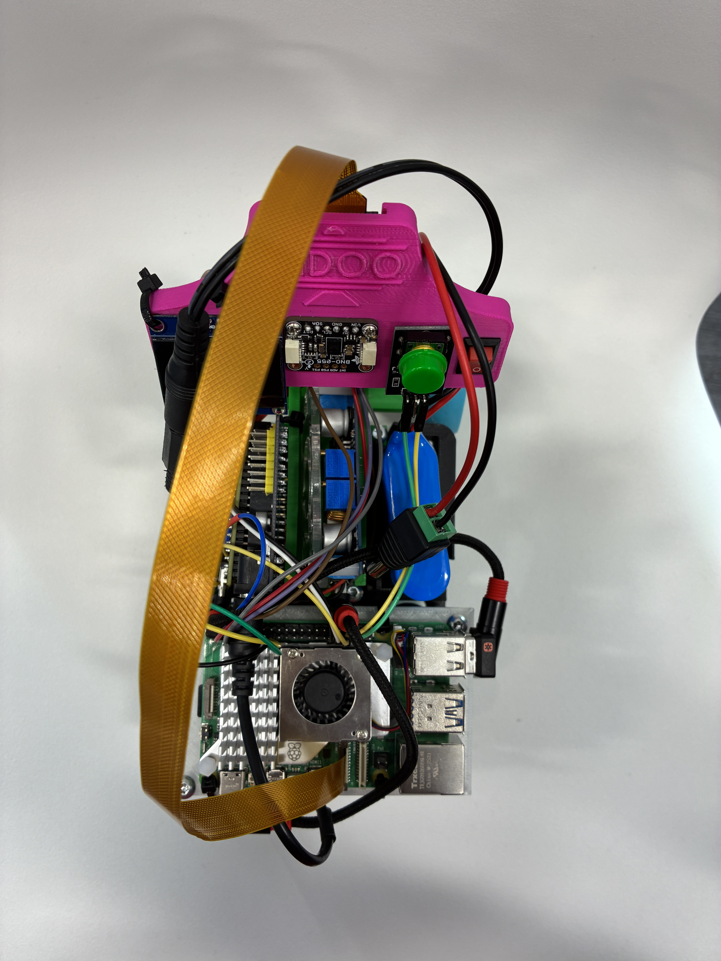
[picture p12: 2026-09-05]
v-photos/robot_top_view.JPG

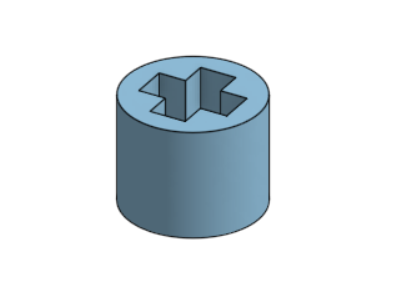
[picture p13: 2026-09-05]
mech/3D_CAD_Files/Axle Spacer.png

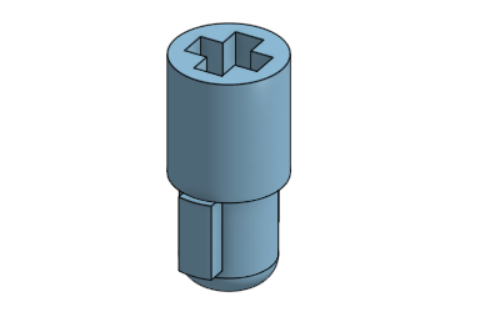
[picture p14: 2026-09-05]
mech/3D_CAD_Files/DifferentialAxleCoupling.png

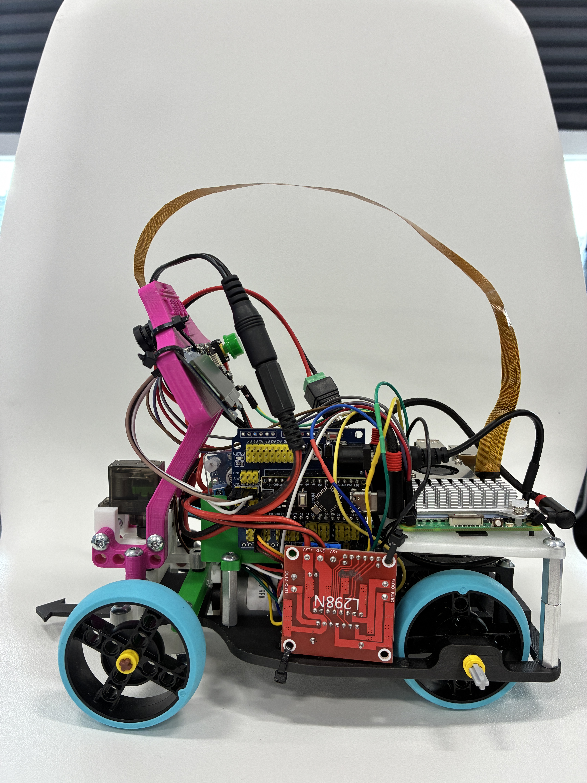
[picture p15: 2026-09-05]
v-photos/robot_left_view.JPG

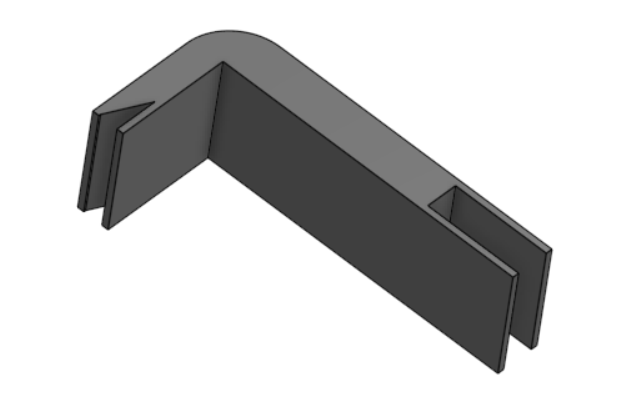
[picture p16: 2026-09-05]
mech/3D_CAD_Files/Battery Holder.png

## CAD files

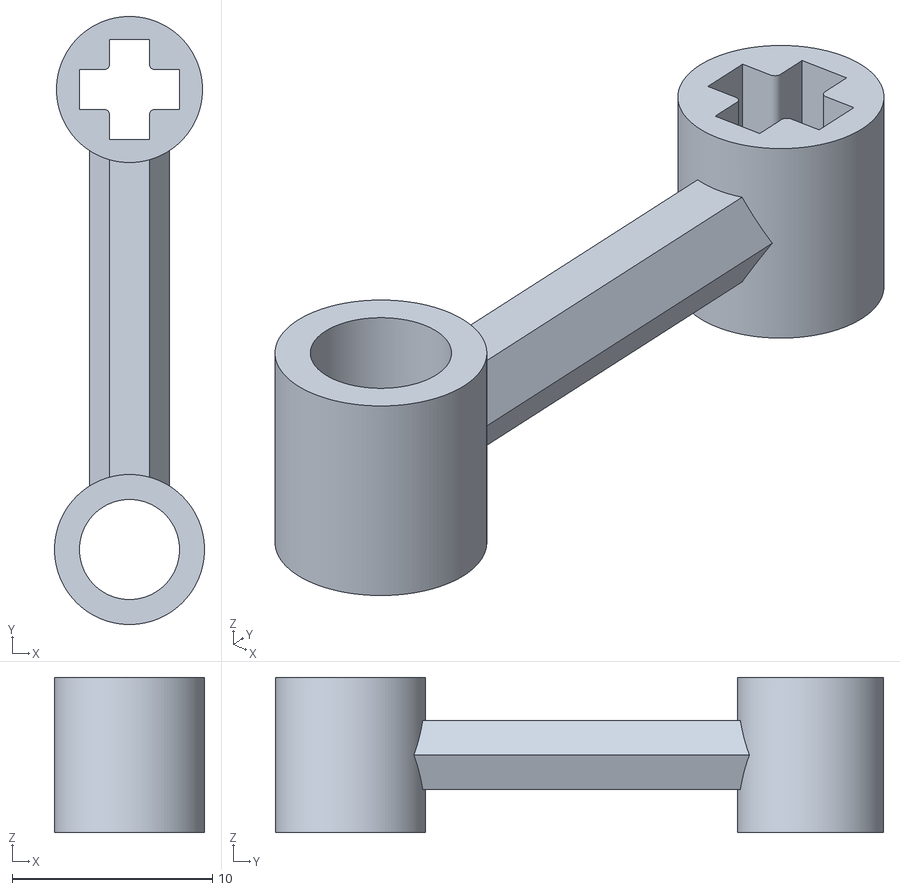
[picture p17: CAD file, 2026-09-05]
mech/3D_CAD_Files/AckermannHexaRod.stl
7.50 x 30.4 x 7.75

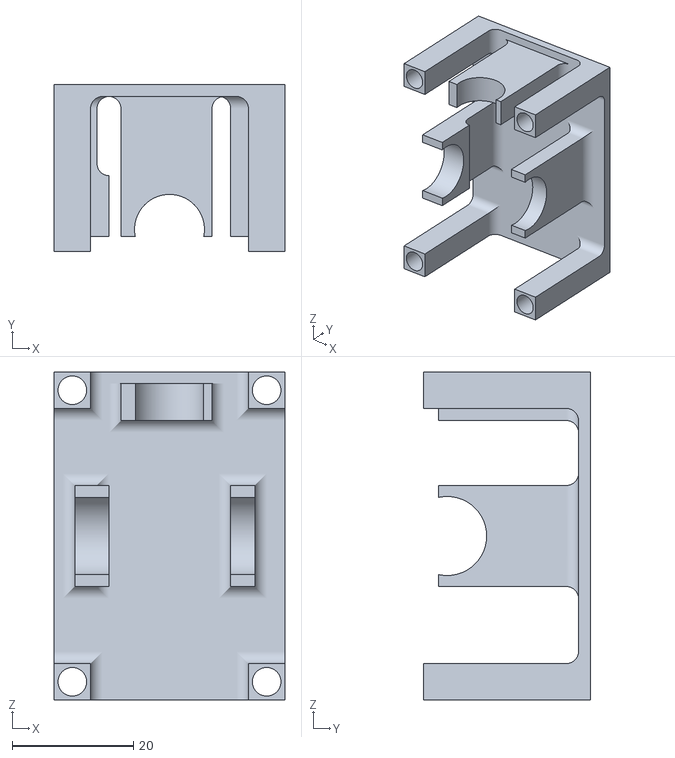
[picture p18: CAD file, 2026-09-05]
mech/3D_CAD_Files/DifferentialHousingV4.stl
38.0 x 27.5 x 54.0

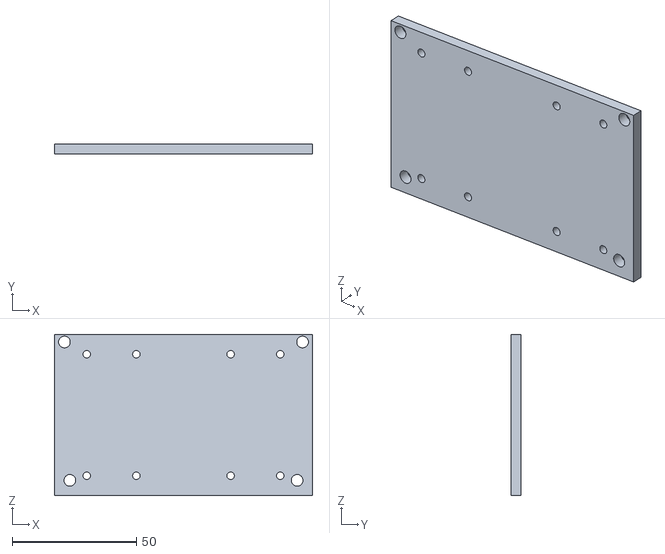
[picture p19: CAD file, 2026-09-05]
mech/3D_CAD_Files/PiPlateV3.stl
104.0 x 4.00 x 65.0

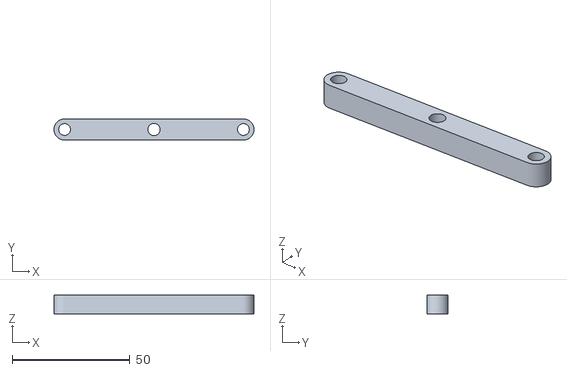
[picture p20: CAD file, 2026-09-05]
mech/3D_CAD_Files/AckermannSRodV2.stl
85.0 x 9.00 x 8.00

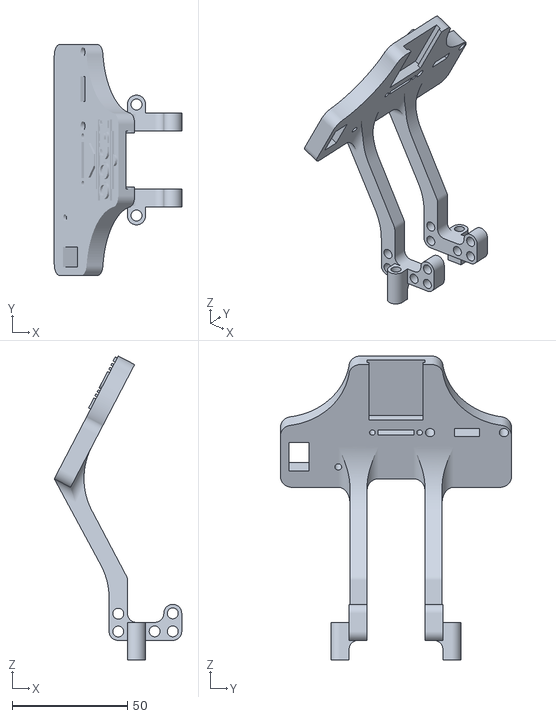
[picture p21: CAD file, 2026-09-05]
mech/3D_CAD_Files/CameraMountV3.stl
55.2 x 100.0 x 131.7

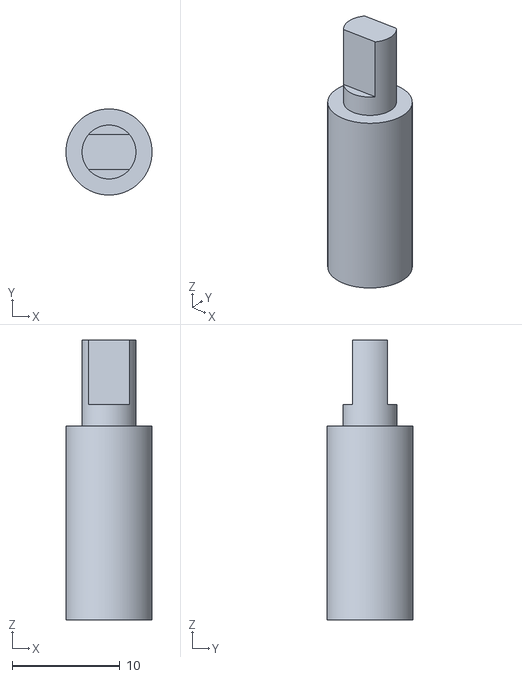
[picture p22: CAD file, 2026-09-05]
mech/3D_CAD_Files/MotorDifferentialCoupling.stl
8.00 x 8.00 x 26.0

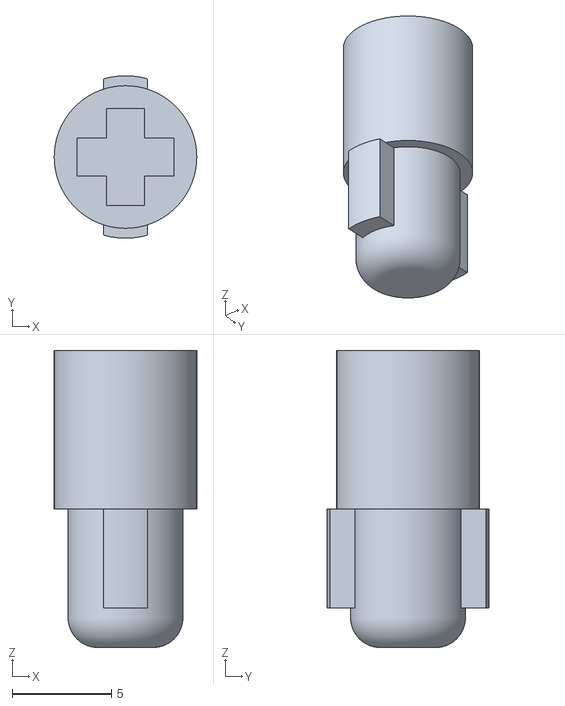
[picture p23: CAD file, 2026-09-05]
mech/3D_CAD_Files/DifferentialAxleCoupling.stl
7.20 x 8.20 x 15.0

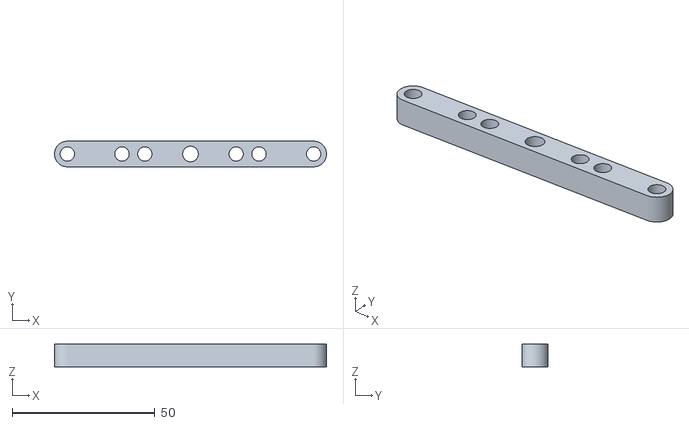
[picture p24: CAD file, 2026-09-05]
mech/3D_CAD_Files/AckermannLRodV3.stl
95.3 x 9.00 x 8.00

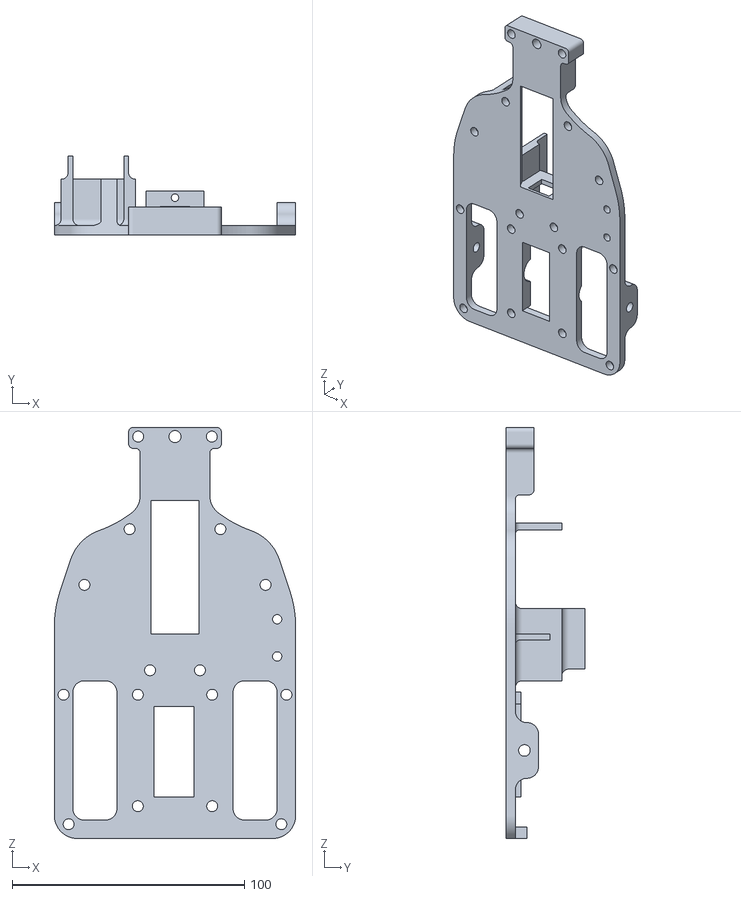
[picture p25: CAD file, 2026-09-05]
mech/3D_CAD_Files/BasePlateV8.stl
104.0 x 34.0 x 177.0

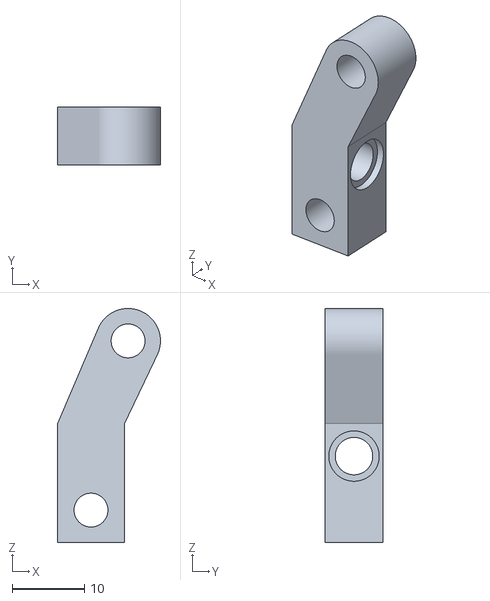
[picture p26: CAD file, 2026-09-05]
mech/3D_CAD_Files/DirectionTabsLH.stl
14.3 x 8.00 x 32.5

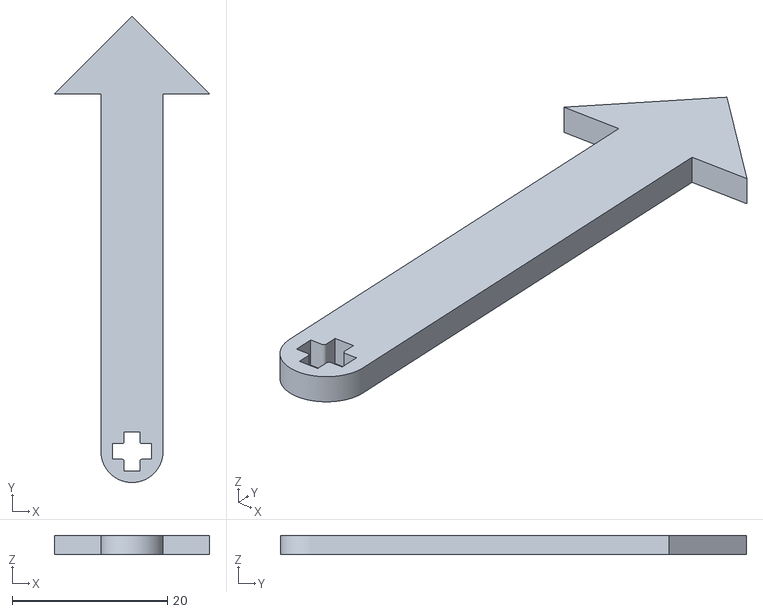
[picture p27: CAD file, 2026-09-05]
mech/3D_CAD_Files/GuideArrowV3.stl
20.0 x 60.0 x 2.50

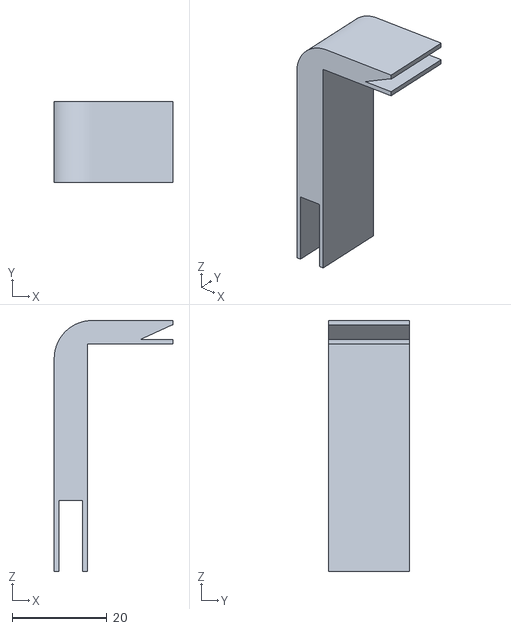
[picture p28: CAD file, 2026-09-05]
mech/3D_CAD_Files/Battery Holder.stl
25.0 x 17.0 x 52.9

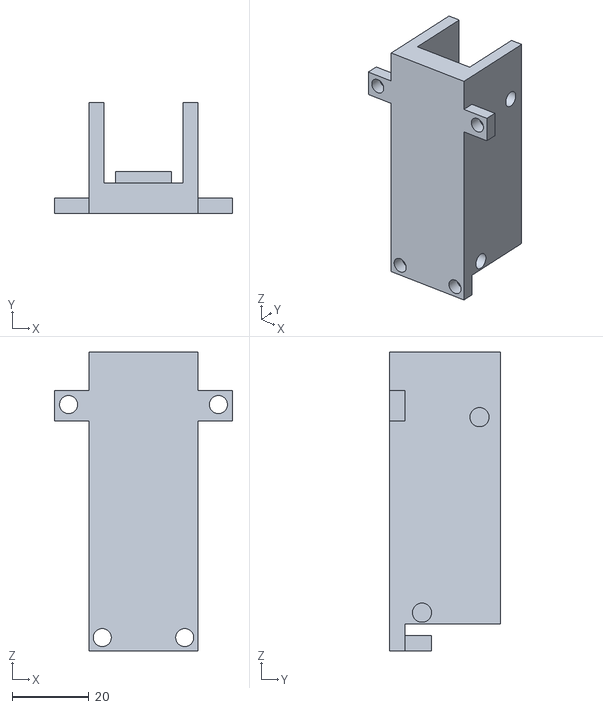
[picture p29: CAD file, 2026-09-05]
mech/3D_CAD_Files/MidPlateV2.stl
46.5 x 29.0 x 78.0

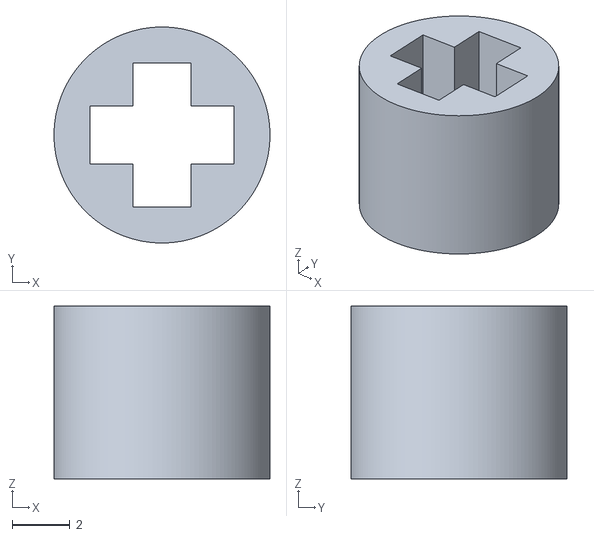
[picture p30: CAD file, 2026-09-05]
mech/3D_CAD_Files/Axle Spacer.stl
7.50 x 7.50 x 6.00

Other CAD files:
mech/3D_CAD_Files/DirectionTabsRH.stl

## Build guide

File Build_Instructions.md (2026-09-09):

# Assembly Instructions

**Step 0: Print the 3D parts**

<details>

<summary> <b><span style="font-size:1.1em; background-color:#f2f2f2; padding:4px 8px; border-radius:5px;">Click here to show the 3D printed parts used in the building process</span></b></summary>

</summary>

| Part Name | Quantity |
| --- | --- |
| Base Plate | 1 |
| Middle Plate | 1 |
| Differential Housing | 1 |
| Pi Plate | 1 |
| Camera-Servo Mount | 1 |
| Ackermann Long Rod | 1 |
| Ackermann Short Rod | 1 |
| Direction Tabs Left Side | 1 |
| Direction Tabs Right Side | 1 |
| Servo Box | 1 |
| Servo-Axle Coupling | 1 |
| Battery Holder | 1 |
| Ackermann Hexagonal Rod | 1 |
| Motor-Differential Coupling | 1 |
| Differential-Axle Coupling | 2 |
| Guide Arrow | 1 |
| WLTOYS 144001 Differential set | 1 |
| Spike Prime wheels | 4 |
| L298N Motor Driver | 1 |
| Arduino Nano with Shield | 1 |
| Raspberry Pi 5 | 1 |
| 12.6V Battery | 1 |
| MG90S Servo | 1 |
| BNO055 IMU | 1 |
| SainSmart Wide-Angle Camera | 1 |
| OLED Display | 1 |
| Start Button | 1 |
| Step-Down Buck Converter | 1 |
| Raspberry Pi 5 | 1 |
| Jumper Wires | 11 |
| Toggle Switch | 1 |
| Raspberry Pi 5 | 1 |
| 1.00 inch VEX Screws | 8 |
| 1.25 inch VEX Screws | 6 |
| 0.375 inch VEX Screws | 10 |
| 1.50 inch VEX Screws | 2 |
| VEX Lock Nuts | 14 |
| 1.00 inch VEX Standoffs | 6 |
| 0.75 inch VEX Standoffs | 2 |
| M2 Screws | 3 |
| M3 Screw | 1 |
| 1.00 inch LEGO shafts | 2 |
| 0.75 inch LEGO shafts with stopper | 2 |
| 1.25 inch LEGO shaft | 1 |
| LEGO Technic connector | 1 |
| LEGO Axle Spacers | 7 |

</details>

Before assembly, prepare the components listed above and print the 3D parts.



**Step 1: Assemble the steering system**

  1. On the edges of the long ackermann steering rod, attach the left and right ackermann tabs with two 1.00 inch VEX screws and lock nuts, positioned such that the tabs are curved inward. Tighten until the tabs don’t shake, but don’t overtighten. The tabs should spin freely.

   

  2. Attach the short ackermann steering rod on the same plane as the long ackermann steering rod, with the same type of two screws and nuts. Same tightening rules.

  
  

  3. Mount the long ackermann steering rod onto the front of the chassis using two 1.25 inch VEX screws and lock nuts, positioned such that the short ackermann rod is facing the back of the chassis and the ackermann tabs are on a lower plane than the long and short ackermann rods.

  
  

  4. Attach the two steering LEGO Spike Prime wheels onto the outsides of the ackermann tabs using two 1.00 inch LEGO axles with stoppers, and two axle spacers.

  
  

  5. Mount the camera and servo mount onto the fixed long ackermann rod using 1.25 inch VEX screws and lock nuts.

  
  

  6. Attach the servo box mount using two 2.00 inch VEX screws and lock nuts, angled such that the servo hole is positioned over the remaining hole in the long ackermann rod. Remember to keep space under the box for the hexagonal ackermann rod.

  
  

  7. Fit a 1.85 inch long LEGO axle into the servo-axle coupling. Thread the axle down through the servo box, through the hexagonal ackermann rod, and through the aforementioned hole. Use a LEGO technic attach piece to attach the other side of the hexagonal ackermann rod to the hole in the middle of the short ackermann rod.

  
  
  
  

  8. Screw in the MG90S servo into the servo box using a ______ M2 screw, with the servo fitted into the servo-axle coupling (MAKE SURE: before you fit the servo, the steering is straight, and the servo angle is 90 degrees. If by human error it is not at 90 degrees, use the servo calibration code provided here (LINK) to figure out the degree at which the servo is straight, which you can change in the main code.

  
  
  

**Step 2: Assemble the drivetrain and chassis body**

  1. Push a 1.575 inch LEGO axle through a LEGO Spike Prime wheel and an axle spacer as shown in the image, then push the axle through the axle hole until the tip of the axle is flush with the wheel. Add an axle spacer on the outside of the chassis. Do the same on the other side.

  
  
  

  2. Push the two differential-axle coupling pieces into the differential sockets such that the ridges on the coupling slide into the valleys on the differential.

  
  

  3. Place the differential into its designated position, with the metal gear on the right side. Then, push the axles into the differential-axle couplings. Might take a little back-and-forth but should slide right in once the right angle is found.

  

  4. Slide the bearing onto the shaft of the pinion and connect the motor-differential coupling. This has a specific alignment but twisting and pushing it should eventually make it fall into place.

  
  

  5. Place the motor in its place with the wires facing upwards. Attach the pinion with the coupling to the motor. This is a tight fit, so it will take some finagling. Ensure the bearing is in its designated semicircle cut and the motor screw hole aligns with the hole in the chassis motor mount. Then screw the motor in using an M2 screw.

  
  

  6. Position the differential housing above the differential such that the bearing clamps are positioned over the three bearings and the holes in the corners go through the chassis. Use four 1.50 inch VEX screws with lock nuts to fasten the housing into place.

  
  
  

  7. In the four holes around the motor, screw in four 1.00 inch standoffs using 0.375 inch VEX screws. Place the middle plate onto the standoffs and screw it in using four more 0.375 inch VEX screws.

  
  
  
  
  
**Mount Electronics**

  1. Using two small zip ties, tighten the arduino nano with its shield onto the side of the middle plate that has holes. 

  

  2. Screw in a 1.00 inch and 0.75 inch standoff on the bottom left and top right holes on the edge of the area around the rear differential, with the two 1.50 inch VEX screw coming up from the bottom of the chassis.

  

  3. Place the Raspberry Pi 5 on the Pi plate. Attach it with four small zip ties to the plate.

  
  

  4. Screw in the Pi plate using two 0.375 inch VEX screws screwed into the standoffs. Make sure the USB-A ports are facing the right side of the robot, the same side as the differential gear.

  
  

  5. Connect the USB-A port on the step-down buck converter to the USB-C port on the Raspberry Pi 5. Also connect the USB-C port on the Arduino Nano to the bottom right port of the Raspberry Pi 5’s USB-A ports.

  

  6. Wire the motor driver and Arduino Nano using the wiring diagram provided above in 2.5.

  
  

  7. With the heatsink facing downwards, zip tie the motor driver onto the chassis using one on the bottom left hole, intersecting with the hole near it, and the top right hole of the motor driver, intersecting with the hole on the Pi plate.

  

  8. Wire the rest of the Raspberry Pi 5 connections using the aforementioned wiring diagram. Plug the 5V power wire from the step-down buck converter into the Arduino Nano.

  

  9. Push the toggle switch into the right most hole on the Control Panel and solder it to the circuit using the wiring diagram, so that the switch controls ALL power going to the robot. 

  

  10. Screw in the BNO055 IMU using two M2 screws on the top two holes, positioned in the middle of the Control Panel. Use zip ties to attach the OLED screen on the left side of the Control Panel, tied through the top two holes. 

  

  11. Screw in the start button into the remaining spot on the Control Panel using an M3 screw. Wire it according to the wiring diagram.

  

  12. Slide the last 3D part, the battery holder, into place as shown in the image below. Make sure the holder is not all the way down because it may rub against the steering wheels. 

  

13. Place the 12.6V battery into its spot and connect the power wire from the 12V side of the step-down buck converter to the corresponding wire on the battery.

  

14. Gently pull up the CSI tab and slide in the Camera wire such that the dark part is facing the tab, then push the tab down to hold the wire in place. Slide the camera upside down into its place on the top front of the Camera mount, with the wire coming out of the top.

  

**Step 3: Upload Software**

1. Connect the Raspberry Pi 5 to your computer.
2. Follow instructions in README.md.

## CONGRATULATIONS!! You have just built your very own self-driving car! Enjoy!



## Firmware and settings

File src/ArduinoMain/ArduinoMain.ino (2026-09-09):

/*==============================================================================
  WRO Future Engineers 2026
  Arduino Nano Firmware

  Purpose:
  Low-level hardware controller for the robot.

  Receives commands from Raspberry Pi:

      steering speed direction lineCount state

  Example:

      100 200 1 4 STR
      120 160 1 5 TUR

  Raspberry Pi ---> Arduino
      steering angle
      motor speed
      driving direction
      detected line count
      competition state

  Arduino:
      - Controls steering servo
      - Controls DC motor through L298N
      - Displays telemetry on OLED
      - Controls NeoPixel status LEDs

==============================================================================*/

//------------------------------------------------------------------------------
// LIBRARIES
//------------------------------------------------------------------------------

#include <Wire.h>
#include <Adafruit_SH110X.h>
#include <Servo.h>
#include <stdio.h>
#include <string.h>

//------------------------------------------------------------------------------
// HARDWARE PIN DEFINITIONS
//------------------------------------------------------------------------------

// Steering servo
#define SERVO_PIN 2

// Built-in Arduino LED
#define LED_PIN 13

// OLED
#define SCREEN_WIDTH 128
#define SCREEN_HEIGHT 64
#define OLED_RESET -1

//------------------------------------------------------------------------------
// SERVO LIMITS
//------------------------------------------------------------------------------

#define SERVO_CENTER 108
#define SERVO_RANGE 60

//------------------------------------------------------------------------------
// SERIAL BUFFER
//------------------------------------------------------------------------------

#define BUFFER_SIZE 16

char inputBuffer[BUFFER_SIZE];
int bufferIndex = 0;

int servo_turn = SERVO_CENTER;
//int speed = 0;
//int dir = 0;
//int line_count = 0;
//char state[5];

//------------------------------------------------------------------------------
// HARDWARE OBJECTS
//------------------------------------------------------------------------------

Adafruit_SH1106G screen(
 SCREEN_WIDTH,
 SCREEN_HEIGHT,
 &Wire,
 OLED_RESET
);

Servo myservo;

//------------------------------------------------------------------------------
// SETUP
//------------------------------------------------------------------------------

void setup() {

  // Motor pins
//  pinMode(MOTOR1, OUTPUT);
//  pinMode(MOTOR2, OUTPUT);
//  pinMode(ENABLEMOT, OUTPUT);

  // Make sure motor is stopped at startup
//  analogWrite(ENABLEMOT, 0);
//  digitalWrite(MOTOR1, LOW);
//  digitalWrite(MOTOR2, LOW);

  // Built-in LED
  pinMode(LED_PIN, OUTPUT);
  digitalWrite(LED_PIN, LOW);

  // Serial communication with Raspberry Pi 
  // Must match Raspberry Pi baud rate.
  Serial.begin(19200);  
  
  // Attach steering servo
  myservo.attach(SERVO_PIN);

  //--------------------------------------------------------------------------
  // OLED INITIALIZATION
  //--------------------------------------------------------------------------

  screen.begin(0x3C, true);

  screen.clearDisplay();
  screen.setTextColor(SH110X_WHITE);
  screen.setTextSize(3);
  screen.setCursor(0, 24);
  screen.print("BOOTING");
  screen.display();

  //--------------------------------------------------------------------------
  // SERVO SELF-TEST AND CENTER
  //--------------------------------------------------------------------------

  myservo.write(SERVO_CENTER-45);
  delay(500);

  myservo.write(SERVO_CENTER);
  delay(300);

  //--------------------------------------------------------------------------
  // READY SCREEN
  //--------------------------------------------------------------------------

  screen.clearDisplay();
  screen.setTextColor(SH110X_WHITE);
  screen.setTextSize(3);
  screen.setCursor(0, 24);
  screen.print("-READY-");
  screen.display();

}


//------------------------------------------------------------------------------
// MAIN LOOP
//------------------------------------------------------------------------------

void loop() {

  /*
     Receive serial data one character at a time.

     The Raspberry Pi sends:

        100 200 1 4 STR\n

     We keep collecting characters until '\n' is received.

     This is more reliable for a real-time robot than
     Serial.readBytesUntil().
  */


  while (Serial.available() > 0) {
  
      char c = Serial.read();
  
      if (c == '\n') {
  
          inputBuffer[bufferIndex] = '\0';
          bufferIndex = 0;
  
          processData(inputBuffer);
      }
      else if (bufferIndex < BUFFER_SIZE - 1) {
  
          inputBuffer[bufferIndex++] = c;
      }
  }
}


//------------------------------------------------------------------------------
// PROCESS SERIAL DATA
//------------------------------------------------------------------------------

void processData(char receivedData[]) {

  /*
     Expected message:

        steering speed direction lineCount state

     Example:

        100 200 1 4 STR

     Values:

        steering
            Servo angle.
            Normally 60-140 for your robot.

        speed
            Motor PWM value.
            0-255.

        direction
            0 = stop
            1 = forward
            2 = reverse

        lineCount
            Number of detected lines.

        state
            STR = STRAIGHT
            TUR = TURNING
  */


  char header;

  //----------------------------------------------------------------------
  // PARSE HEADER
  //----------------------------------------------------------------------
  
  int parsed = sscanf(
      receivedData,
      " %c",
      &header
  );
  
  
  //----------------------------------------------------------------------
  // INVALID HEADER
  //----------------------------------------------------------------------
  
  if (parsed != 1) {
      return;
  }
  
  
  //----------------------------------------------------------------------
  // HANDLE MESSAGE TYPE
  //----------------------------------------------------------------------
  
  //--------------------------------------------------------------------------
  // HANDLE MESSAGE TYPE
  //--------------------------------------------------------------------------

  switch (header) {

    //======================================================================
    // # = TURN ON BUILT-IN LED
    // Expected:
    // #
    //======================================================================

    case '#':

      char msg[5];

      parsed = sscanf(
        receivedData,
        " # %4s",
        &msg
      );

      if (parsed != 1) {
        return;
      }

      digitalWrite(LED_PIN, HIGH);
      screen.setTextColor(SH110X_WHITE);
      screen.clearDisplay();
      screen.setTextSize(3);
      screen.setCursor(30, 20);
      screen.print(msg);
      screen.display();
      

      return;


    //======================================================================
    // $ = SERVO VALUE
    // Expected:
    // $ servo_turn
    //======================================================================

    case '$':

      parsed = sscanf(
        receivedData,
        " $ %d",
        &servo_turn
      );

      if (parsed != 1) {
        return;
      }

      // Safety limit
      servo_turn = constrain(
        servo_turn,
        SERVO_CENTER - SERVO_RANGE,
        SERVO_CENTER + SERVO_RANGE
      );

      // Set servo
      myservo.write(servo_turn);

      return;


    //======================================================================
    // UNKNOWN HEADER
    //======================================================================

    default:

      return;
  }
  }
  
  
  //--------------------------------------------------------------------------
  // OLED TELEMETRY
  //--------------------------------------------------------------------------

//  myservo.write(servo_turn);

//  driveMotor(speed,dir);
 
//  screen.clearDisplay();
// 
//  screen.setTextColor(SH110X_WHITE);
//  
//  // Servo
//  screen.setTextSize(2);
//  screen.setCursor(2, 2);
//  screen.print(servo_turn);
//  
//   //Separator
//  screen.drawFastVLine(
//    40,
//    0,
//    20,
//    SH110X_WHITE
//  );
// 
//  // Line count
//  screen.setCursor(44, 2);
//  screen.print(line_count);
// 
//  //Separator
//  screen.drawFastVLine(
//    70,
//    0,
//    20,
//    SH110X_WHITE
//  );
// 
//  // Speed
//  screen.setCursor(75, 2);
//  screen.print(speed);
//  
//  //Horizontal separator
//  screen.drawFastHLine(
//    0,
//    20,
//    128,
//    SH110X_WHITE
//  );
// 
//  // State
//  screen.setTextSize(3);
//  screen.setCursor(0, 30);
//  screen.print(state);
// 
//  //Motor direction
//  screen.drawFastVLine(
//    80,
//    20,
//    44,
//    SH110X_WHITE
//  );
// 
//  //--------------------------------------------------------------------------
//  // UPDATE OLED ONCE
//  //--------------------------------------------------------------------------
// 
//  screen.display();
  
//}


//------------------------------------------------------------------------------
// MOTOR CONTROL
//------------------------------------------------------------------------------

//void driveMotor(int speed, int dir) {
//
//  /*
//     L298N motor control:
//
//        dir = 0
//            STOP
//
//        dir = 1
//            FORWARD
//
//        dir = 2
//            REVERSE
//  */
//
//  screen.setTextSize(3);
//  screen.setCursor(90, 30);
//
//  //--------------------------------------------------------------------------
//  // FORWARD
//  //--------------------------------------------------------------------------
//
//  if (dir == 1) {
//
//    analogWrite(
//      ENABLEMOT,
//      speed
//    );
//
//    digitalWrite(
//      MOTOR1,
//      LOW
//    );
//
//    digitalWrite(
//      MOTOR2,
//      HIGH
//    );
//
//    screen.print(">>");
//  }
//
//
//  //--------------------------------------------------------------------------
//  // REVERSE
//  //--------------------------------------------------------------------------
//
//  else if (dir == 2) {
//
//    analogWrite(
//      ENABLEMOT,
//      speed
//    );
//
//    digitalWrite(
//      MOTOR1,
//      HIGH
//    );
//
//    digitalWrite(
//      MOTOR2,
//      LOW
//    );
//
//    screen.print("<<");
//  }
//
//
//  //--------------------------------------------------------------------------
//  // STOP
//  //--------------------------------------------------------------------------
//
//  else {
//
//    analogWrite(
//      ENABLEMOT,
//      0
//    );
//
//    digitalWrite(
//      MOTOR1,
//      LOW
//    );
//
//    digitalWrite(
//      MOTOR2,
//      LOW
//    );
//
//    screen.print("XX");
//  }
//
//  // IMPORTANT:
//  // OLED is NOT updated here.
//  //
//  // processData() calls screen.display()
//  // once after all telemetry is drawn.
//}

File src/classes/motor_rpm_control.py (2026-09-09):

"""
Single-file RPM-controlled DC motor driver for a Raspberry Pi + L298N.

Hardware:

    L298N pin      Raspberry Pi GPIO (BCM numbering)
    ---------      ---------------------------------
    IN1        ->  GPIO 5      (direction bit 1)
    IN2        ->  GPIO 6      (direction bit 2)
    ENA        ->  GPIO 13     (PWM speed control)

    Encoder A  ->  GPIO 17
    Encoder B  ->  GPIO 27
"""

import time
from gpiozero import RotaryEncoder, PWMOutputDevice, DigitalOutputDevice


# ============================================================
# PIN CONFIGURATION
# ============================================================

# --- Motor driver (L298N) ---
IN1_PIN = 5
IN2_PIN = 6
ENA_PIN = 13
PWM_FREQUENCY = 1000  # Hz

# --- Encoder ---
ENCODER_A_PIN = 17
ENCODER_B_PIN = 27


# ============================================================
# DRIVETRAIN / ENCODER CONSTANTS
# ============================================================

GEARBOX_RATIO = 9.6
DIFFERENTIAL_RATIO = 2.5
ENCODER_PPR = 11        # Hall pulses per motor revolution (datasheet)
QUADRATURE = 4          # gpiozero RotaryEncoder counts x4 per cycle

# Theoretical steps per WHEEL revolution -- CALIBRATE THIS
#STEPS_PER_WHEEL_REV = ENCODER_PPR * QUADRATURE * GEARBOX_RATIO * DIFFERENTIAL_RATIO
# = 1056
# Calibrated separately per direction -- backward has its own backlash/traction/encoder-edge
# behavior, so it doesn't necessarily match forward's measured steps/rev. If driveRotations(...,
# 'BWD') stops short of the real distance, raise STEPS_PER_WHEEL_REV_BWD (more counted steps
# required per commanded rotation); if it overshoots, lower it.
STEPS_PER_WHEEL_REV_FWD = 125
STEPS_PER_WHEEL_REV_BWD = 175


# Reference only, not enforced anywhere below.
GEARBOX_OUTPUT_RPM_NO_LOAD = 620
MAX_WHEEL_RPM_NO_LOAD = GEARBOX_OUTPUT_RPM_NO_LOAD / DIFFERENTIAL_RATIO
# ~= 248 RPM no-load; expect less once the robot's weight/friction loads the motor.

# ============================================================
# CONTROL LOOP SETTINGS
# ============================================================

CONTROL_PERIOD = 0.05  # seconds between controller updates

# Uncomment / tune once you've measured your motor's dead zone:
# MIN_RUNNING_PWM = 70
MIN_RUNNING_PWM = 0

# ============================================================
# ENCODER / RPM MEASUREMENT
# ============================================================

class EncoderRPM:
    def __init__(self, pin_a, pin_b, steps_per_rev):
        self.encoder = RotaryEncoder(pin_a, pin_b, max_steps=0)
        self.steps_per_rev = steps_per_rev

        self.last_count = self.encoder.steps
        self.last_time = time.monotonic()
        self.rpm = 0.0

    def update(self):
        now = time.monotonic()
        count = self.encoder.steps

        dt = now - self.last_time
        delta = count - self.last_count

        self.last_count = count
        self.last_time = now

        if dt <= 0:
            return self.rpm

        revolutions = delta / self.steps_per_rev
        raw_rpm = revolutions / dt * 60.0
        self.rpm = abs(raw_rpm)
        return self.rpm

    def get_count(self):
        return self.encoder.steps

    def reset(self):
        self.last_count = self.encoder.steps
        self.last_time = time.monotonic()
        self.rpm = 0.0

    def close(self):
        self.encoder.close()


# ============================================================
# PID SPEED CONTROLLER  (operates in 0-255 "virtual PWM" units)
# ============================================================

class RPMController:
    """
    output = kp*error + ki*integral(error) + kd*d(error)/dt

    Tune kp, then ki, then kd -- one gain at a time.
    """

    def __init__(self, kp, ki, kd, min_pwm, max_pwm):
        self.kp = kp   # main push term, proportional to current error
        self.ki = ki   # closes steady-state error from friction/load
        self.kd = kd   # damps overshoot; noisy at low RPM, tune last

        self.min_pwm = min_pwm
        self.max_pwm = max_pwm

        self.integral = 0.0
        self.prev_error = 0.0
        self.output = 0.0

    def update(self, target_rpm, current_rpm, dt):
        if target_rpm <= 0:
            self.reset()
            return 0

        error = target_rpm - current_rpm

        derivative = (error - self.prev_error) / dt if dt > 0 else 0.0
        self.prev_error = error

        # only commit this cycle's integral if it doesn't push output past the PWM limits
        # (anti-windup: freezing the integral on saturation avoids overshoot once it clears)
        tentative_integral = self.integral + error * dt
        raw_output = (
            self.kp * error
            + self.ki * tentative_integral
            + self.kd * derivative
        )

        if self.min_pwm <= raw_output <= self.max_pwm:
            self.integral = tentative_integral

        self.output = max(self.min_pwm, min(self.max_pwm, raw_output))

        return int(round(self.output))

    def reset(self):
        self.integral = 0.0
        self.prev_error = 0.0
        self.output = 0.0

# ============================================================
# MOTOR DRIVER  (direct L298N control, no Arduino / no serial)
# ============================================================

class MotorDriver:
    def __init__(self, in1_pin, in2_pin, ena_pin, pwm_frequency=1000):
        self.in1 = DigitalOutputDevice(in1_pin)
        self.in2 = DigitalOutputDevice(in2_pin)
        self.ena = PWMOutputDevice(ena_pin, frequency=pwm_frequency)

    def drive(self, pwm_0_255, direction):
        """direction: "FWD", "BWD", or "STOP" """
        pwm_0_255 = max(0, min(255, int(pwm_0_255)))
        duty = pwm_0_255 / 255.0

        if direction == "FWD" and pwm_0_255 > 0:
            self.in2.on()
            self.in1.off()
            self.ena.value = duty
        elif direction == "BWD" and pwm_0_255 > 0:
            self.in2.off()
            self.in1.on()
            self.ena.value = duty
        else:
            self.stop()

    def stop(self):
        self.ena.value = 0
        self.in1.off()
        self.in2.off()

    def close(self):
        self.stop()
        self.in1.close()
        self.in2.close()
        self.ena.close()


# ============================================================
# SHARED OBJECTS  (one motor, one encoder, one controller)
# ============================================================

encoder = EncoderRPM(ENCODER_A_PIN, ENCODER_B_PIN, STEPS_PER_WHEEL_REV_FWD)
controller = RPMController(kp=1.5, ki=20, kd=0.0, min_pwm=0, max_pwm=255)
motor = MotorDriver(IN1_PIN, IN2_PIN, ENA_PIN, PWM_FREQUENCY)


# ============================================================
# maintainRPM -- the main thing you call from your program
# ============================================================
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
